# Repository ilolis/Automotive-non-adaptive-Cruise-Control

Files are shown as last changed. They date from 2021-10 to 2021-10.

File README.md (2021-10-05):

# Automotive Non Adaptive Cruise Control retrofit for cars
Specifically designed for a Nissan Micra K12 but can be adapted to other cars with existing PCB and firmware changes. 
**DEVICE UNDER DEVELOPMENT. DO NOT USE IT IN A CAR.**

## Description
The goal of this project is to design an aftermarket KIT that is able to hold the specified speed of a car. 

## How it works
**Inputs**

 - Abs speed sensor signal for measuring speed
 - Brake light signal to detect when brake pedal is pressed
 - Actual accelerator pedal signal 
- Various Buttons for controlling the Cruise Control 

**Outputs**
- The accelerator pedal signal that is routed to the car ECU
- Various indicator lights

How it works:

 -  If the Cruise Control is OFF, the actual accelerator pedal signal is routed to the ECU without the intervention of the KIT. 
 - If the Cruise Control is ON, the Arduino reads the speed of the vehicle through the Speed Sensors and generates the correct pedal signal so that the vehicle maintains set speed. The generated (fake) pedal signal is then routed to the ECU.
 - A MUX is used that outputs either the real accelerator pedal signal (when Cruise Control is disabled) or the (fake) signal of the Arduino (if Cruise Control is enabled).  
 - Two relays connected in series act as a MUX while also providing redundancy. In case one relay is stuck the real accelerator pedal will always be routed to the output.
 - The brake pedal deactivates the Cruise Control and immediately (via hardware logic) changes the Select signal of the MUX so that the output changes to the real accelerator pedal. The system will always switch the output to the real accelerator pedal even if the Arduino is frozen. 

## Status
I am currently testing the board, the functionality works as expected with the prototypes. Never use it in car since it is not 100% tested and I can not guarantee that it works flawlessly. Severe injury can be made. More testing has to be done. Software will be the next step.

## License 
Copyright 2021 Lolis Ilias

Permission is hereby granted, free of charge, to any person obtaining a copy of this software and associated documentation files (the "Software"), to deal in the Software without restriction, including without limitation the rights to use, copy, modify, merge, publish, distribute, sublicense, and/or sell copies of the Software, and to permit persons to whom the Software is furnished to do so, subject to the following conditions:

The above copyright notice and this permission notice shall be included in all copies or substantial portions of the Software.

THE SOFTWARE IS PROVIDED "AS IS", WITHOUT WARRANTY OF ANY KIND, EXPRESS OR IMPLIED, INCLUDING BUT NOT LIMITED TO THE WARRANTIES OF MERCHANTABILITY, FITNESS FOR A PARTICULAR PURPOSE AND NONINFRINGEMENT. IN NO EVENT SHALL THE AUTHORS OR COPYRIGHT HOLDERS BE LIABLE FOR ANY CLAIM, DAMAGES OR OTHER LIABILITY, WHETHER IN AN ACTION OF CONTRACT, TORT OR OTHERWISE, ARISING FROM, OUT OF OR IN CONNECTION WITH THE SOFTWARE OR THE USE OR OTHER DEALINGS IN THE SOFTWARE.

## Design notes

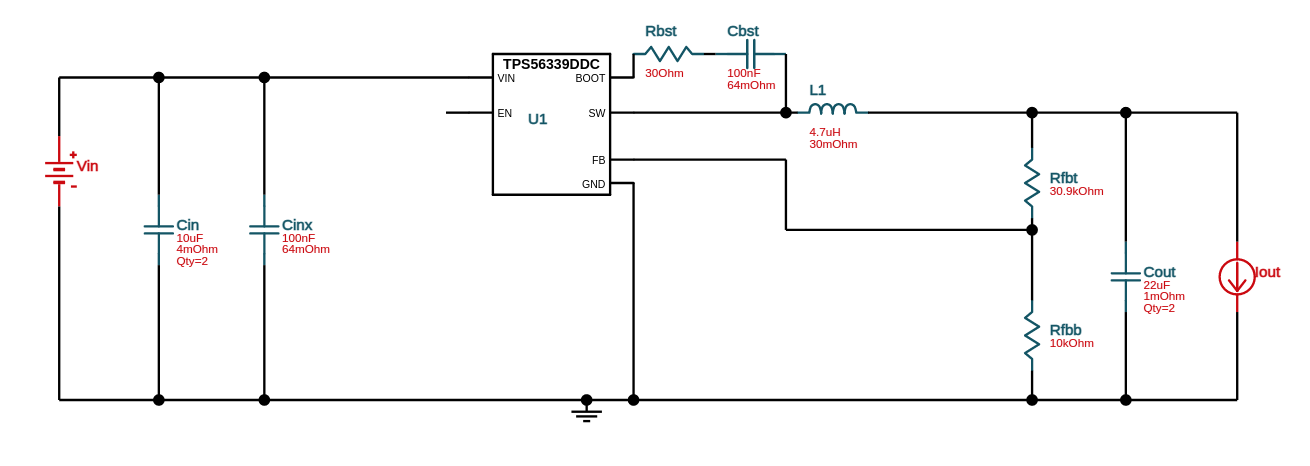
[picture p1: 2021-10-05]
Kicad Schematics/Other/Webench.png

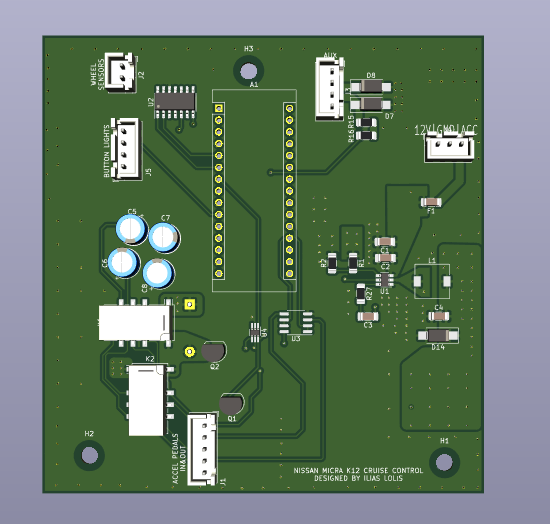
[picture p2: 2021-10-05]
3D Model Front.png

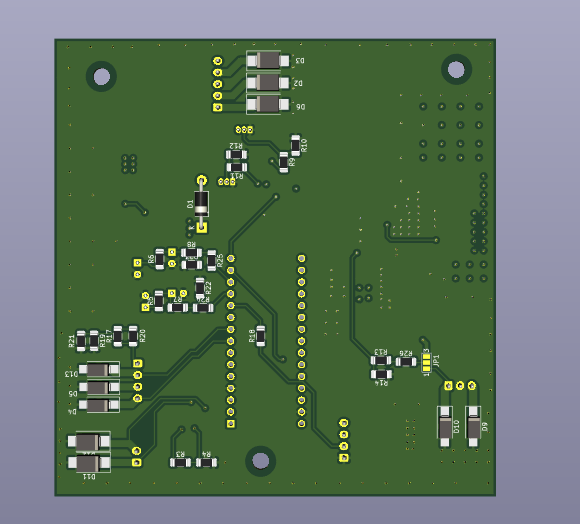
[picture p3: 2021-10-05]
3D Model Bottom.png

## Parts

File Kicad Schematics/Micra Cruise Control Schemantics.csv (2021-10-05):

Reference | Quantity | Value | Footprint | Datasheet | LCSC no | MPN
C1 | 1 | 10uF | Capacitor_SMD:C_1206_3216Metric_Pad1.33x1.80mm_HandSolder | ~ |  | JMK316BJ106KL-T
C2 C3 | 2 | 100nF | Capacitor_SMD:C_1206_3216Metric_Pad1.33x1.80mm_HandSolder | ~ |  | CC1206KRX7R9BB104
C4 | 1 | 22uF | Capacitor_SMD:C_1206_3216Metric_Pad1.33x1.80mm_HandSolder | ~ |  | JMK316BJ226KL-T
C5 C6 | 2 | 2.2uF | Capacitor_THT:CP_Radial_D6.3mm_P2.50mm | ~ | C357599
C7 C8 | 2 | 100uF | Capacitor_THT:CP_Radial_D6.3mm_P2.50mm | ~ | C47891
D1 | 1 | 1N4004 | Diode_THT:D_DO-41_SOD81_P10.16mm_Horizontal | http://www.vishay.com/docs/88503/1n4001.pdf | C331630
D2 D3 D6 D11 D12 | 5 | SMBJ17A | Diode_SMD:D_SMB_Handsoldering |  | C353382
D4 D5 D7 D8 D13 D14 | 6 | SMAJ6.0A | Diode_SMD:D_SMA_Handsoldering |  | C693555
D9 D10 | 2 | SMBJ22A | Diode_SMD:D_SMA_Handsoldering |  | C440288
F1 | 1 | 150mA | Capacitor_SMD:C_1206_3216Metric_Pad1.33x1.80mm_HandSolder | ~ | C369153
K1 K2 | 2 | G6S-2 | Relay_SMD:Relay_DPDT_Omron_G6S-2F | http://omronfs.omron.com/en_US/ecb/products/pdf/en-g6s.pdf |  | G6S-2F DC5
L1 | 1 | 4.7uH | Inductor_SMD:L_7.3x7.3_H3.5 | ~ |  | YPRH0703-4R7M
Q1 | 1 | 2N3904 | Package_TO_SOT_THT:TO-92_Inline | https://www.onsemi.com/pub/Collateral/2N3903-D.PDF | C305395
Q2 | 1 | 2N7000 | Package_TO_SOT_THT:TO-92_Inline | https://www.onsemi.com/pub/Collateral/NDS7002A-D.PDF | C232838
R17 R19 R20 R21 | 4 | 270Ω | Resistor_SMD:R_1206_3216Metric_Pad1.30x1.75mm_HandSolder | ~ |  | 1206W4J0271T5E
R22 R25 | 2 | 4.98k | Resistor_SMD:R_1206_3216Metric_Pad1.30x1.75mm_HandSolder | ~ |  | 1206W4F4991T5E
R23 R24 | 2 | 2.49k | Resistor_SMD:R_1206_3216Metric_Pad1.30x1.75mm_HandSolder | ~ |  | 1206W4F2491T5E
R26 R1 | 1 | 30.9k | Resistor_SMD:R_1206_3216Metric_Pad1.30x1.75mm_HandSolder | ~ |  | 1206W4F3092T5E
R27 | 1 | 30Ω | Resistor_SMD:R_1206_3216Metric_Pad1.30x1.75mm_HandSolder | ~ |  | 1206W4J0300T5E
R3 | 1 | 5kΩ | Resistor_SMD:R_1206_3216Metric_Pad1.30x1.75mm_HandSolder | ~ |  | 1206W4F4991T5E
R4 R5 R6 R7 R8 R11 R15 R16 R18 | 9 | 1kΩ | Resistor_SMD:R_1206_3216Metric_Pad1.30x1.75mm_HandSolder | ~ |  | 1206W4F1001T5E
R9 R10 R12 R13 R14 R2 | 6 | 10kΩ | Resistor_SMD:R_1206_3216Metric_Pad1.30x1.75mm_HandSolder | ~ |  | 1206W4F1002T5E
U1 | 1 | TPS56339DDC | Package_TO_SOT_SMD:TSOT-23-6 | https://www.ti.com/lit/ds/symlink/tps56339.pdf |  | TPS56339DDCR
U2 | 1 | LM339 | Package_SO:SOIC-14_3.9x8.7mm_P1.27mm | https://www.st.com/resource/en/datasheet/lm139.pdf | C71036
U3 | 1 | LM358 | Package_SO:SOP-8_3.76x4.96mm_P1.27mm | http://www.ti.com/lit/ds/symlink/lm2904-n.pdf | C74525
U4 | 1 | NL7SZ57DFT2G | Package_TO_SOT_SMD:SOT-363_SC-70-6_Handsoldering |  | C94398 | NL7SZ57DFT2G
RX | 1 | 100kΩ | Resistor_SMD:R_1206_3216Metric_Pad1.30x1.75mm_HandSolder | ~ |  | 1206W4F1003T5E

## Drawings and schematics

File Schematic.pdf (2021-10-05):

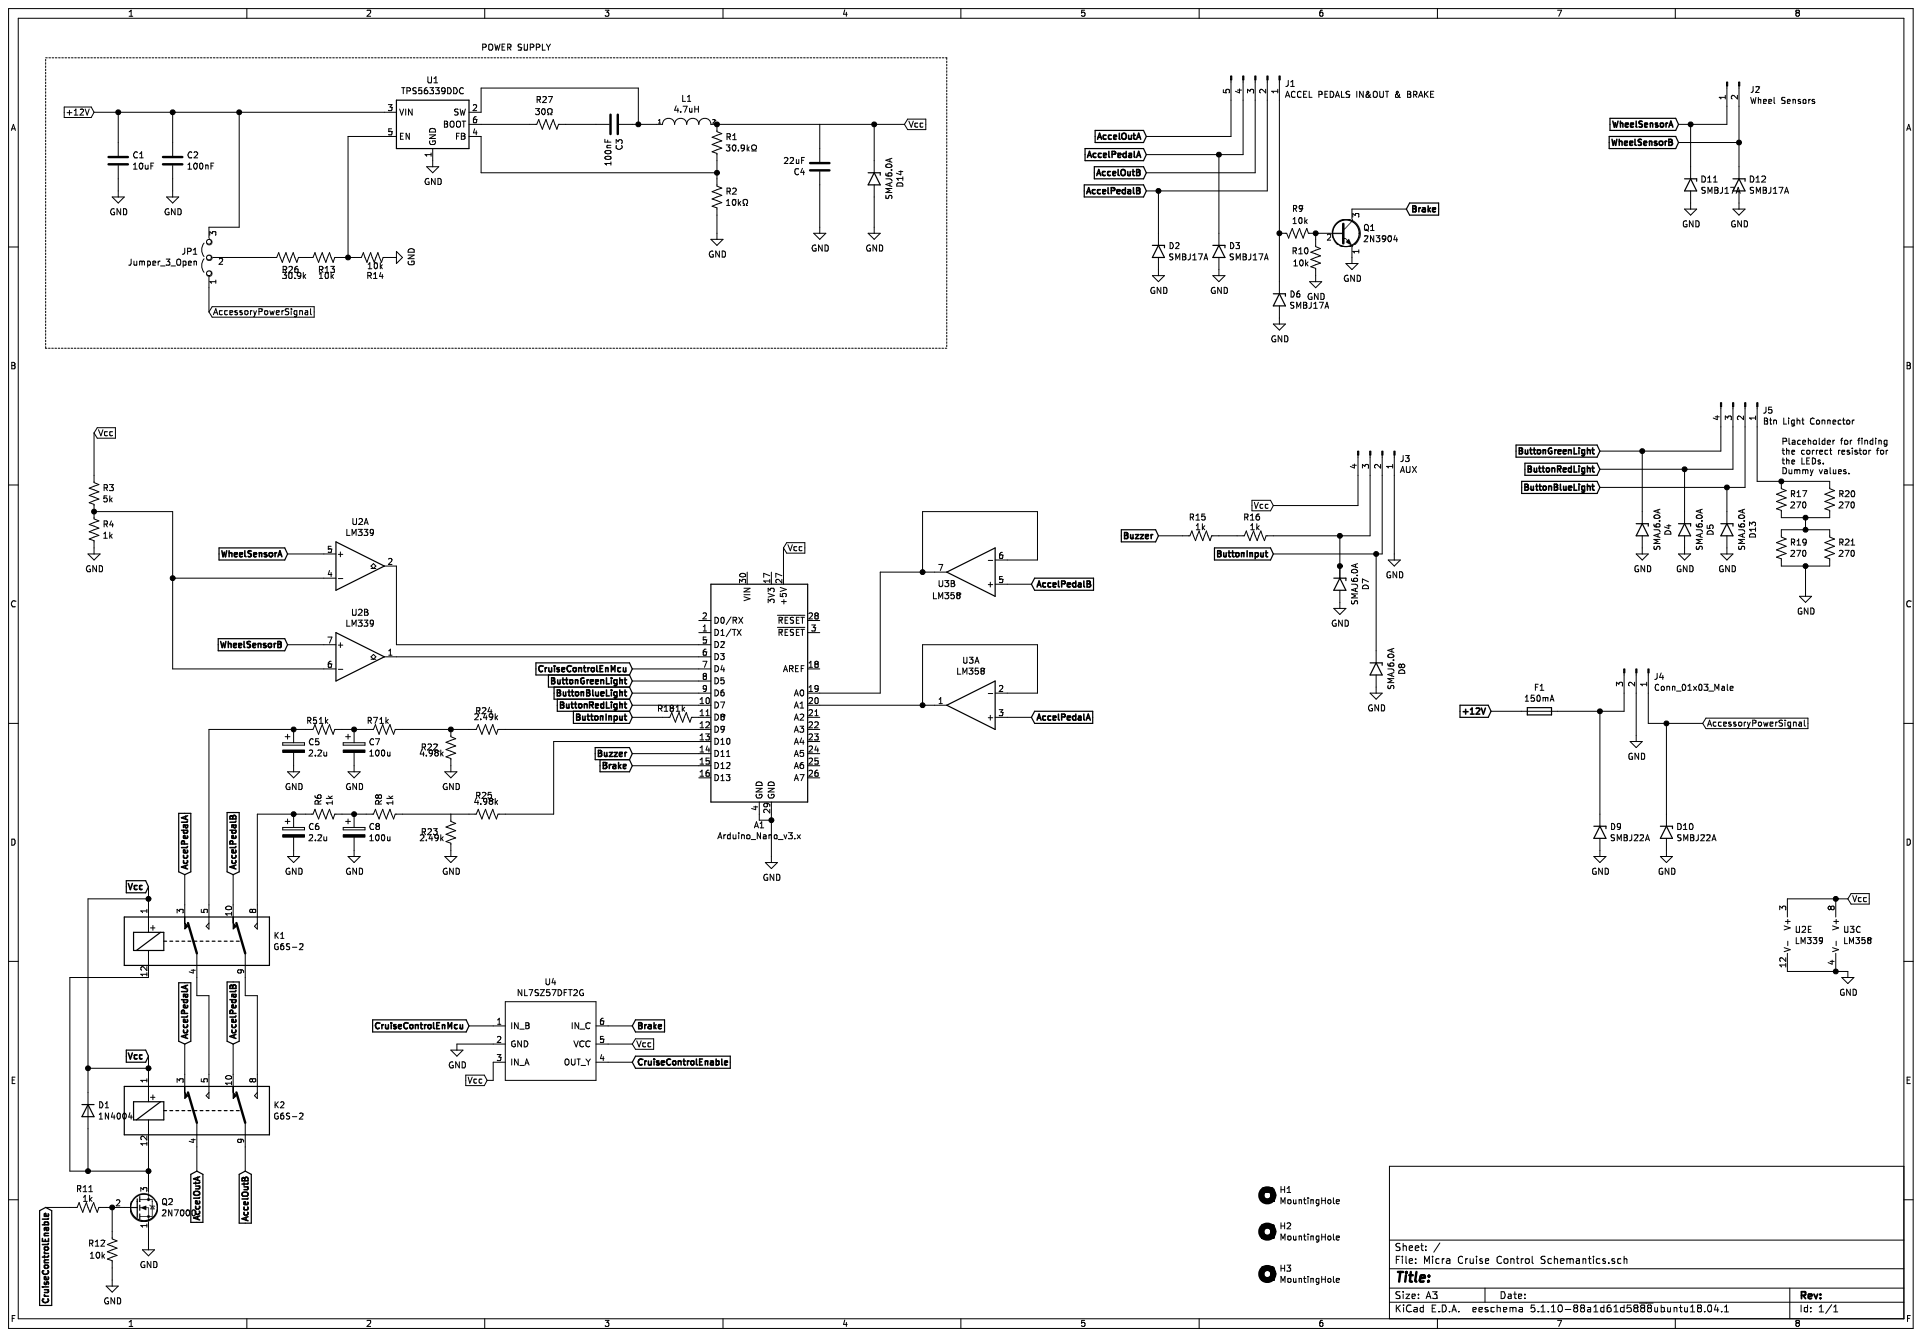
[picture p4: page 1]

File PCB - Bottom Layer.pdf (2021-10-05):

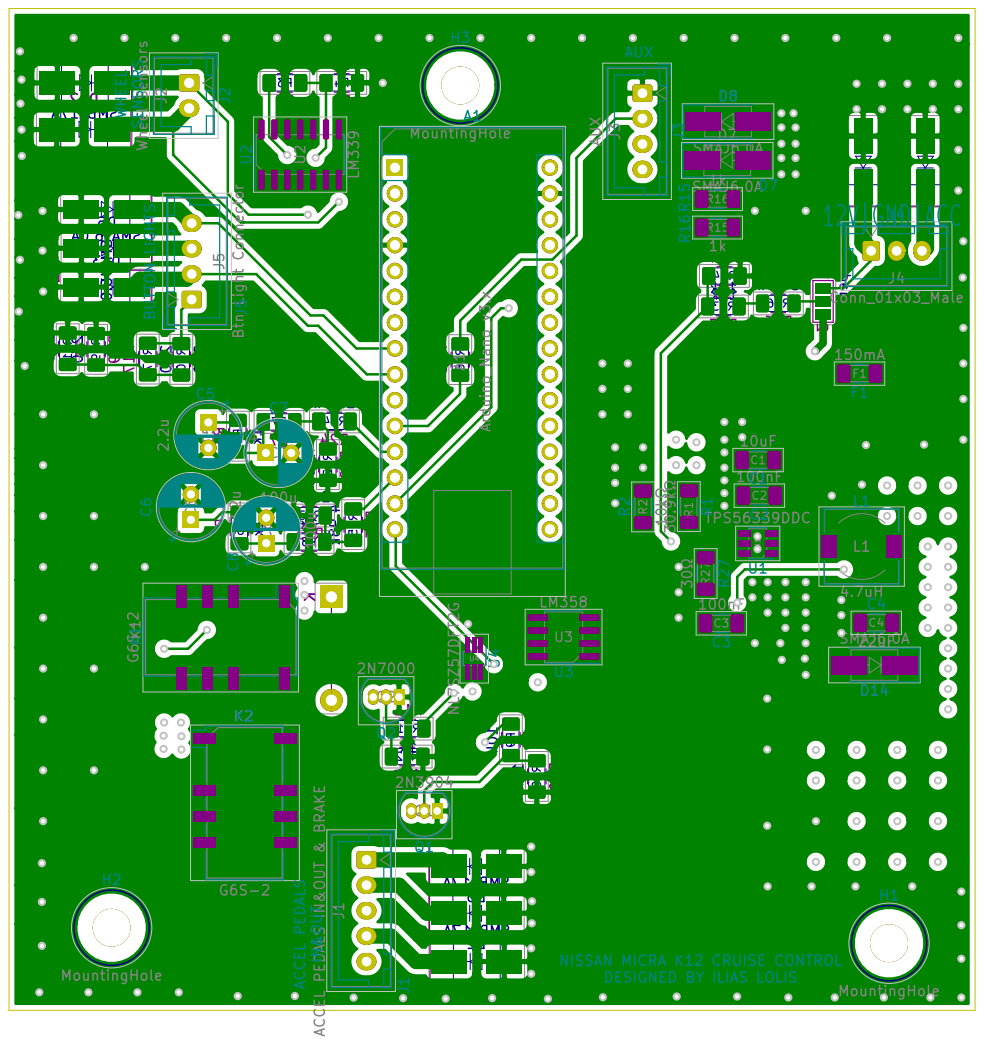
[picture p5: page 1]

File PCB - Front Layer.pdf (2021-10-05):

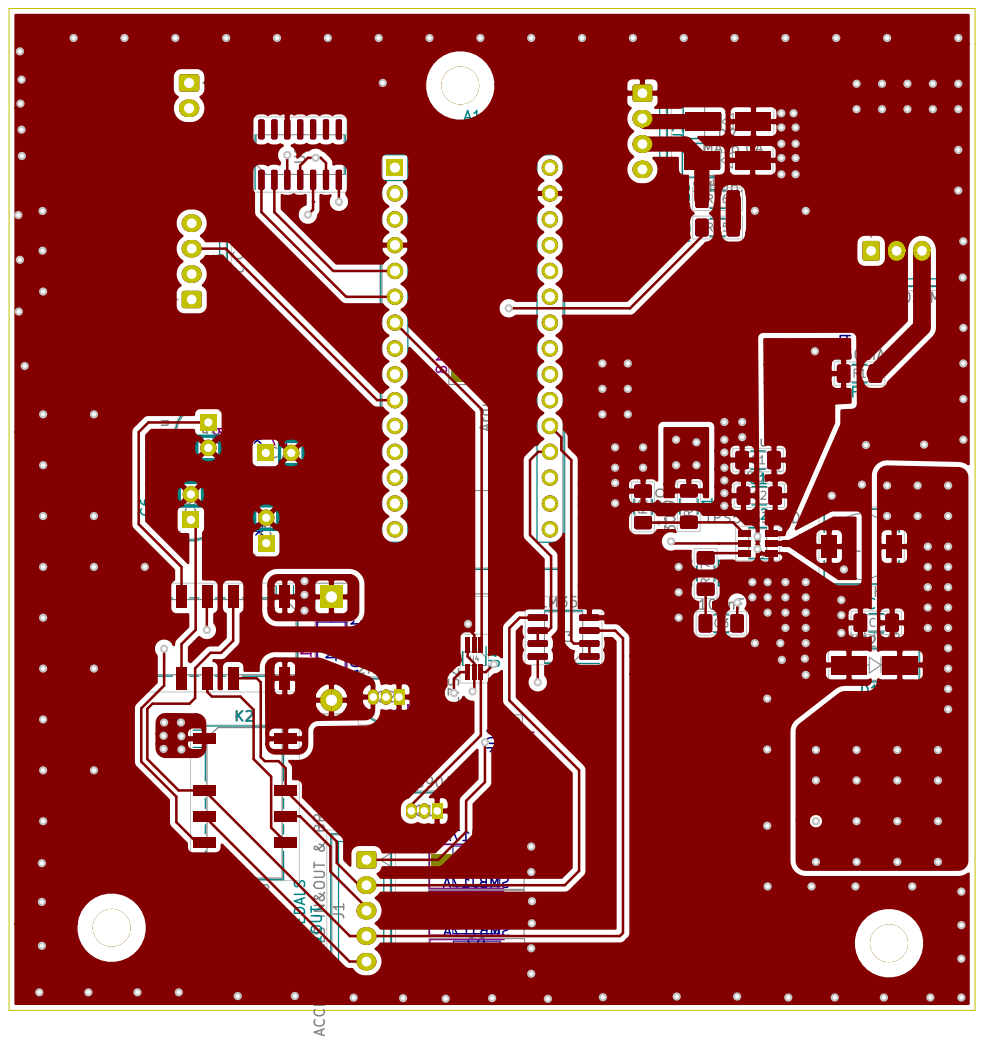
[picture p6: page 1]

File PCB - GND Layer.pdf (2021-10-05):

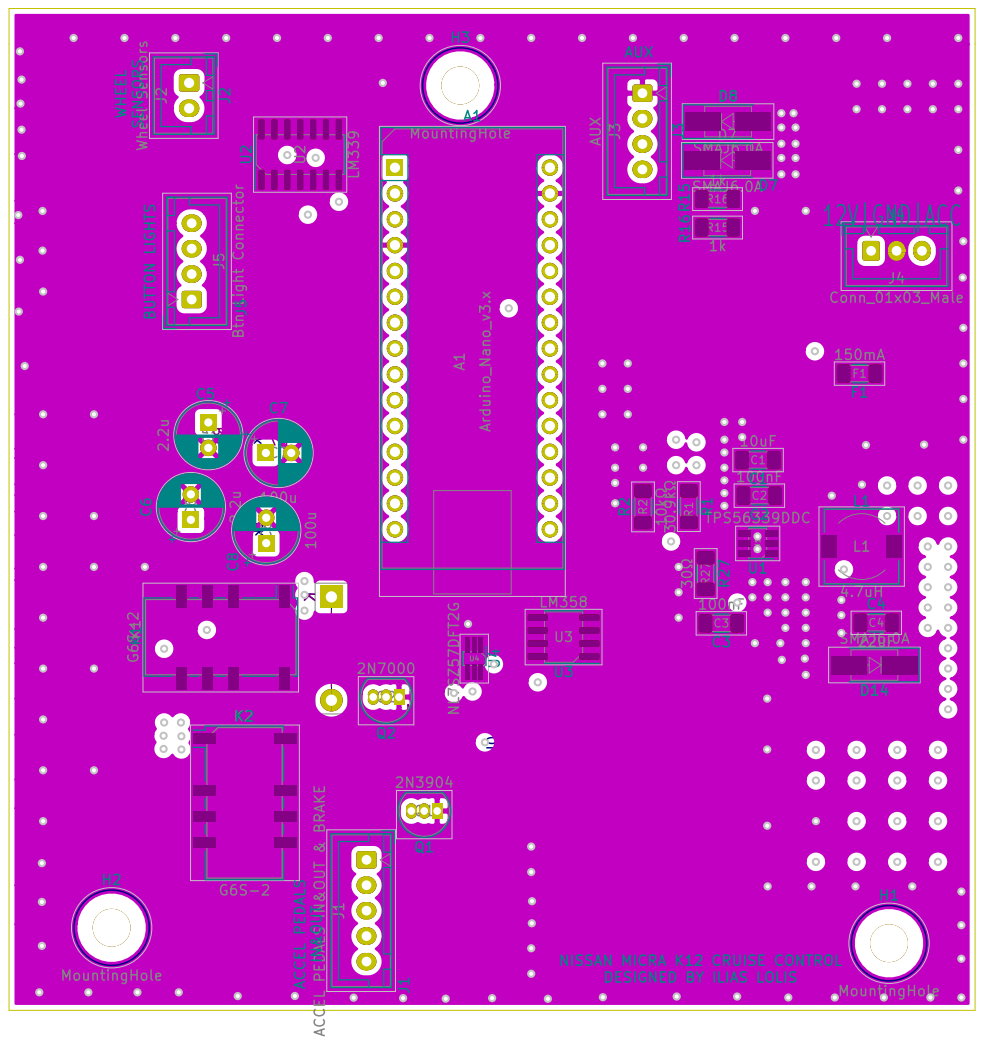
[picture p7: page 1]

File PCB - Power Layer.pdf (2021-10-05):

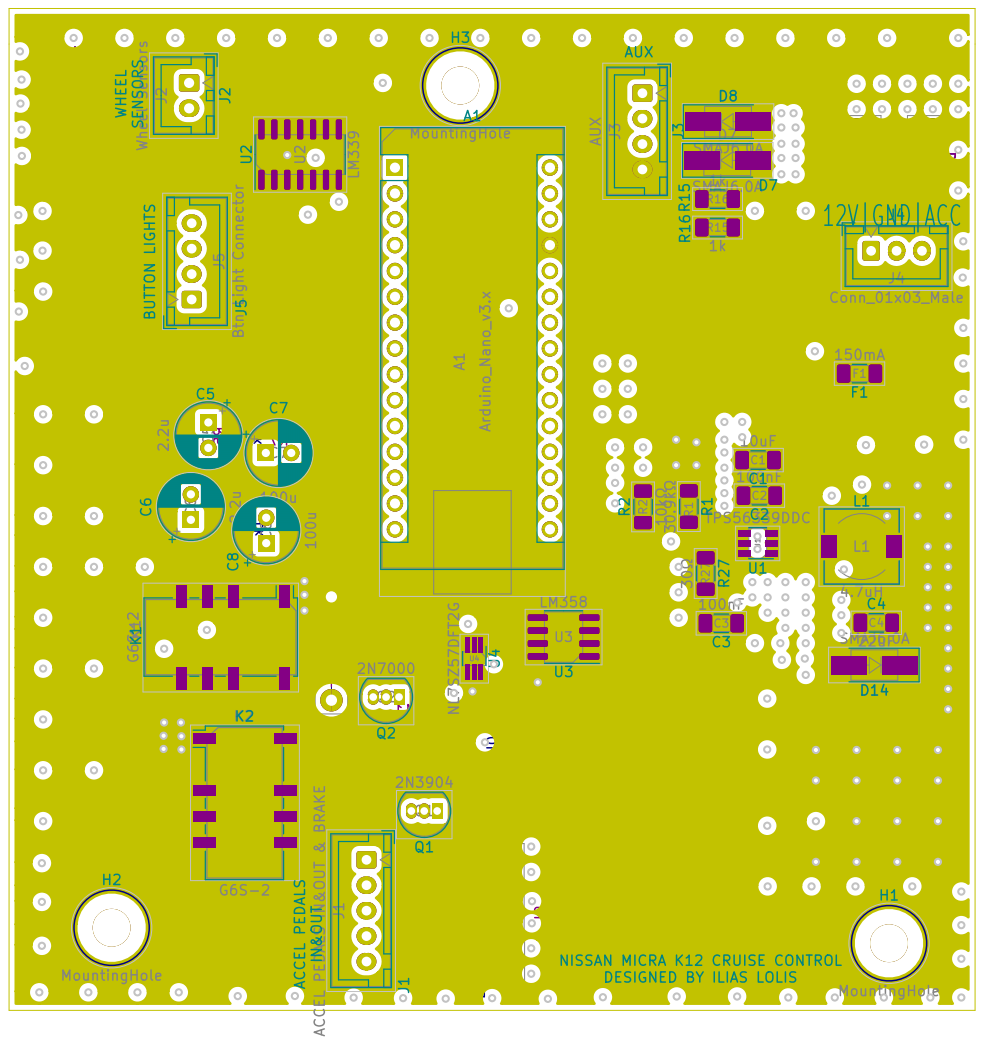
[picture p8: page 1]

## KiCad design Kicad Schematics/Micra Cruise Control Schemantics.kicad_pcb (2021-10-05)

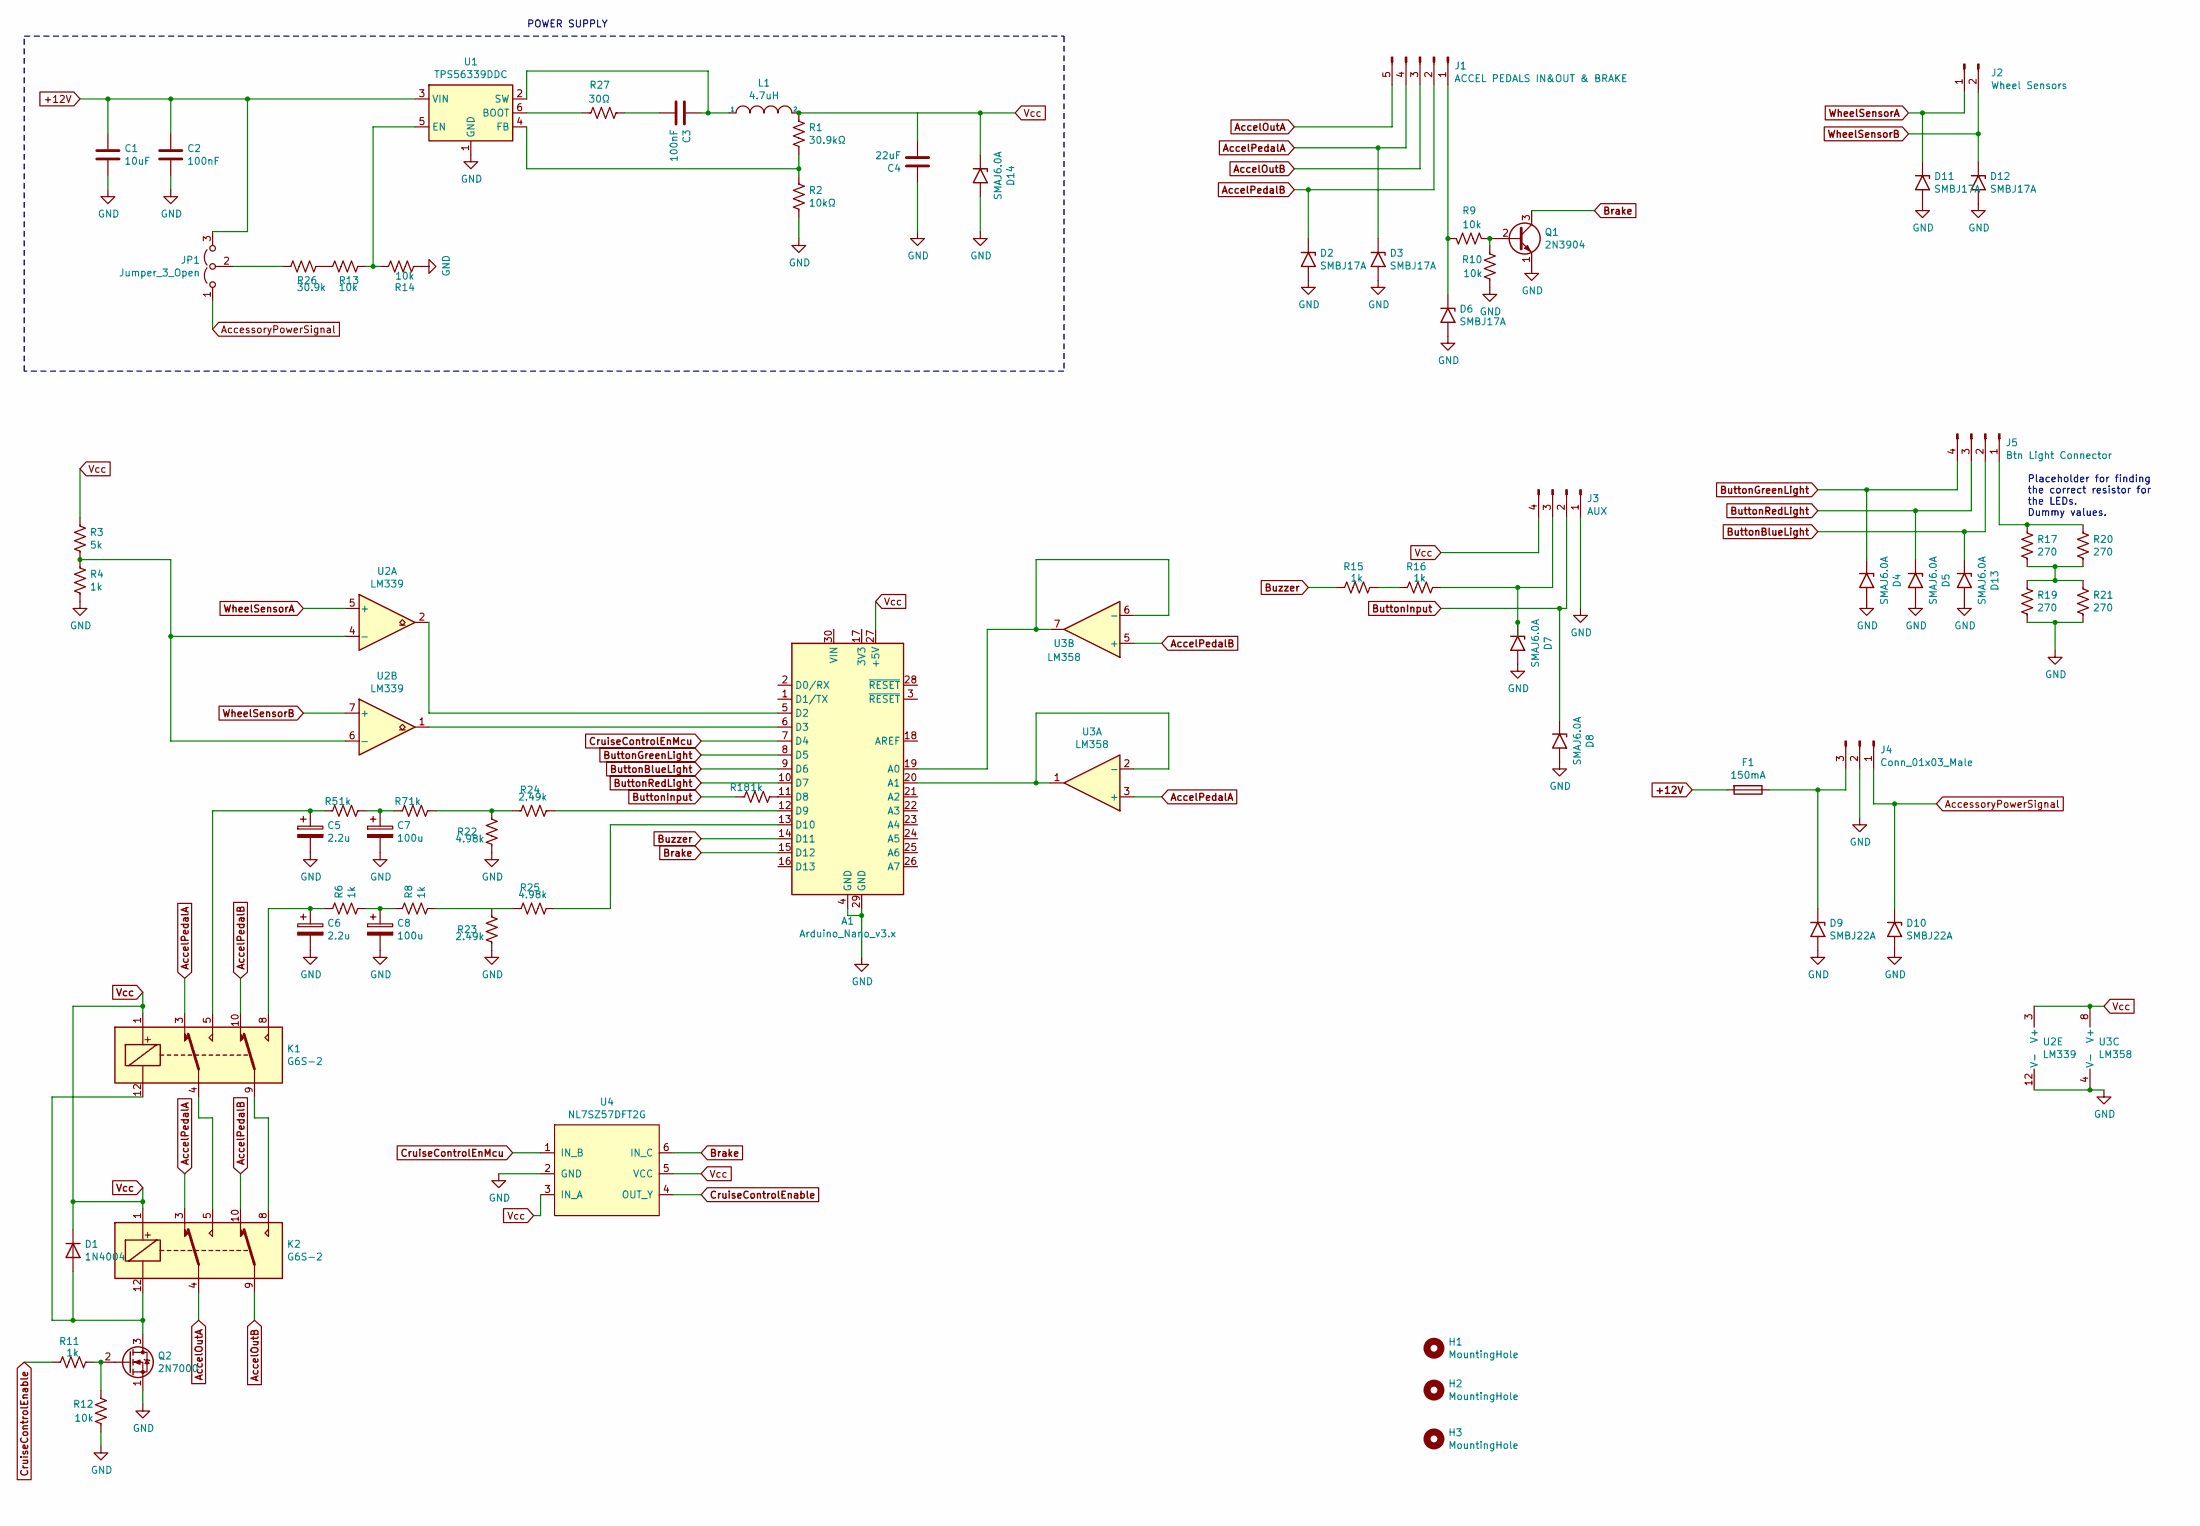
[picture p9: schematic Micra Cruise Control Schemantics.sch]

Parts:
A1: Arduino_Nano_v3.x; Arduino_Nano
C1: 10uF; C_1206_3216Metric_Pad1.33x1.80mm_HandSolder
C2, C3: 100nF; C_1206_3216Metric_Pad1.33x1.80mm_HandSolder
C4: 22uF; C_1206_3216Metric_Pad1.33x1.80mm_HandSolder
C5: 2.2u; CP_Radial_D6.3mm_P2.50mm
C6: 2.2u; CP_Radial_D6.3mm_P2.50mm; PartNo EGS2GM2R2E09OT
C7, C8: 100u; CP_Radial_D6.3mm_P2.50mm; PartNo ERS1EM101E11OT
D1: 1N4004; D_DO-41_SOD81_P10.16mm_Horizontal
D2, D3, D6, D11, D12: SMBJ17A; D_SMB_Handsoldering
D4, D5, D7, D8, D13, D14: SMAJ6.0A; D_SMA_Handsoldering
D9, D10: SMBJ22A; D_SMA_Handsoldering
F1: 150mA; C_1206_3216Metric_Pad1.33x1.80mm_HandSolder; LCSC no C369153
H1, H2, H3: MountingHole; MountingHole_3.7mm
J1: ACCEL PEDALS IN&OUT & BRAKE; JST_XH_B5B-XH-A_1x05_P2.50mm_Vertical
J2: Wheel Sensors; JST_XH_B2B-XH-A_1x02_P2.50mm_Vertical
J3: AUX; JST_XH_B4B-XH-A_1x04_P2.50mm_Vertical
J4: Conn_01x03_Male; JST_XH_B3B-XH-A_1x03_P2.50mm_Vertical
J5: Btn Light Connector; JST_XH_B4B-XH-A_1x04_P2.50mm_Vertical
JP1: Jumper_3_Open; SolderJumper-3_P1.3mm_Open_Pad1.0x1.5mm_NumberLabels
K1, K2: G6S-2; Relay_DPDT_Omron_G6S-2F; PartNo G6S-2F DC5
L1: 4.7uH; L_7.3x7.3_H3.5; Part Number YPRH0703-4R7M
Q1: 2N3904; TO-92_Inline; LCSC no C305395
Q2: 2N7000; TO-92_Inline; LCSC no C232838
R1: 30.9kΩ; R_1206_3216Metric_Pad1.30x1.75mm_HandSolder
R2: 10kΩ; R_1206_3216Metric_Pad1.30x1.75mm_HandSolder
R3: 5k; R_1206_3216Metric_Pad1.30x1.75mm_HandSolder
R4, R5, R6, R7, R8, R11, R15, R16, R18: 1k; R_1206_3216Metric_Pad1.30x1.75mm_HandSolder
R9, R10, R12, R13, R14: 10k; R_1206_3216Metric_Pad1.30x1.75mm_HandSolder
R17, R19, R20, R21: 270; R_1206_3216Metric_Pad1.30x1.75mm_HandSolder
R22, R25: 4.98k; R_1206_3216Metric_Pad1.30x1.75mm_HandSolder
R23, R24: 2.49k; R_1206_3216Metric_Pad1.30x1.75mm_HandSolder
R26: 30.9k; R_1206_3216Metric_Pad1.30x1.75mm_HandSolder
R27: 30Ω; R_1206_3216Metric_Pad1.30x1.75mm_HandSolder
U1: TPS56339DDC; TSOT-23-6; MPN TPS56339DDCR
U2: LM339; SOIC-14_3.9x8.7mm_P1.27mm; LCSC no C71036
U3: LM358; SOP-8_3.76x4.96mm_P1.27mm; LCSC no C74525
U4: NL7SZ57DFT2G; SOT-363_SC-70-6_Handsoldering; MPN NL7SZ57DFT2G; LCSC no C94398

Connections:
+12V: C1.1, C2.1, F1.2, JP1.3 (B), U1.3 (VIN)
AccelOutA: J1.5, K2.4
AccelOutB: J1.3, K2.9
AccelPedalA: D3.1 (A1), J1.4, K1.3, K2.3, U3.3 (+)
AccelPedalB: D2.1 (A1), J1.2, K1.10, K2.10, U3.5 (+)
AccessoryPowerSignal: D10.1 (A1), J4.1, JP1.1 (A)
Brake: A1.15 (D12), Q1.3 (C), U4.6 (IN_C)
ButtonBlueLight: A1.9 (D6), D13.1 (A1), J5.2
ButtonGreenLight: A1.8 (D5), D4.1 (A1), J5.4
ButtonInput: D8.1 (A1), J3.2, R18.1
ButtonRedLight: A1.10 (D7), D5.1 (A1), J5.3
Buzzer: A1.14 (D11), R15.1
CruiseControlEnMcu: A1.7 (D4), U4.1 (IN_B)
CruiseControlEnable: R11.1, U4.4 (OUT_Y)
GND: A1.4 (GND), A1.29 (GND), C1.2, C2.2, C4.1, C5.2, C6.2, C7.2, C8.2, D2.2 (A2), D3.2 (A2), D4.2 (A2), D5.2 (A2), D6.2 (A2), D7.2 (A2), D8.2 (A2), D9.2 (A2), D10.2 (A2), D11.2 (A2), D12.2 (A2), D13.2 (A2), D14.2 (A2), J3.1, J4.2, Q1.1 (E), Q2.1 (S), R2.2, R4.2, R10.1, R12.1, R14.1, R19.2, R21.2, R22.1, R23.1, U1.1 (GND), U2.12 (V-), U3.4 (V-), U4.2 (GND)
unnamed: A1.5 (D2), U2.2
unnamed: A1.6 (D3), U2.1
unnamed: A1.11 (D8), R18.2
unnamed: A1.12 (D9), R24.2
unnamed: A1.13 (D10), R25.2
unnamed: A1.19 (A0), U3.6 (-), U3.7
unnamed: A1.20 (A1), U3.1, U3.2 (-)
unnamed: C3.1, L1.1, U1.2 (SW)
unnamed: C3.2, R27.2
unnamed: C5.1, K1.5, R5.1
unnamed: C6.1, K1.8, R6.1
unnamed: C7.1, R5.2, R7.1
unnamed: C8.1, R6.2, R8.1
unnamed: D1.2 (A), K1.12, K2.12, Q2.3 (D)
unnamed: D6.1 (A1), J1.1, R9.2
unnamed: D7.1 (A1), J3.3, R16.2
unnamed: D9.1 (A1), F1.1, J4.3
unnamed: J5.1, R17.1, R20.1
unnamed: JP1.2 (C), R26.2
unnamed: K1.4, K2.5
unnamed: K1.9, K2.8
unnamed: Q1.2 (B), R9.1, R10.2
unnamed: Q2.2 (G), R11.2, R12.2
unnamed: R1.2, R2.1, U1.4 (FB)
unnamed: R3.2, R4.1, U2.4 (-), U2.6 (-)
unnamed: R13.1, R14.2, U1.5 (EN)
unnamed: R13.2, R26.1
unnamed: R15.2, R16.1
unnamed: R17.2, R19.1, R20.2, R21.1
unnamed: R7.2, R22.2, R24.1
unnamed: R8.2, R23.2, R25.1
unnamed: R27.1, U1.6 (BOOT)
Vcc: A1.27 (+5V), C4.2, D1.1 (K), D14.1 (A1), J3.4, K1.1, K2.1, L1.2, R1.1, R3.1, U2.3 (V+), U3.8 (V+), U4.3 (IN_A), U4.5 (VCC)
WheelSensorA: D11.1 (A1), J2.1, U2.5 (+)
WheelSensorB: D12.1 (A1), J2.2, U2.7 (+)

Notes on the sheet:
Placeholder for finding the correct resistor for the LEDs. Dummy values.
POWER SUPPLY

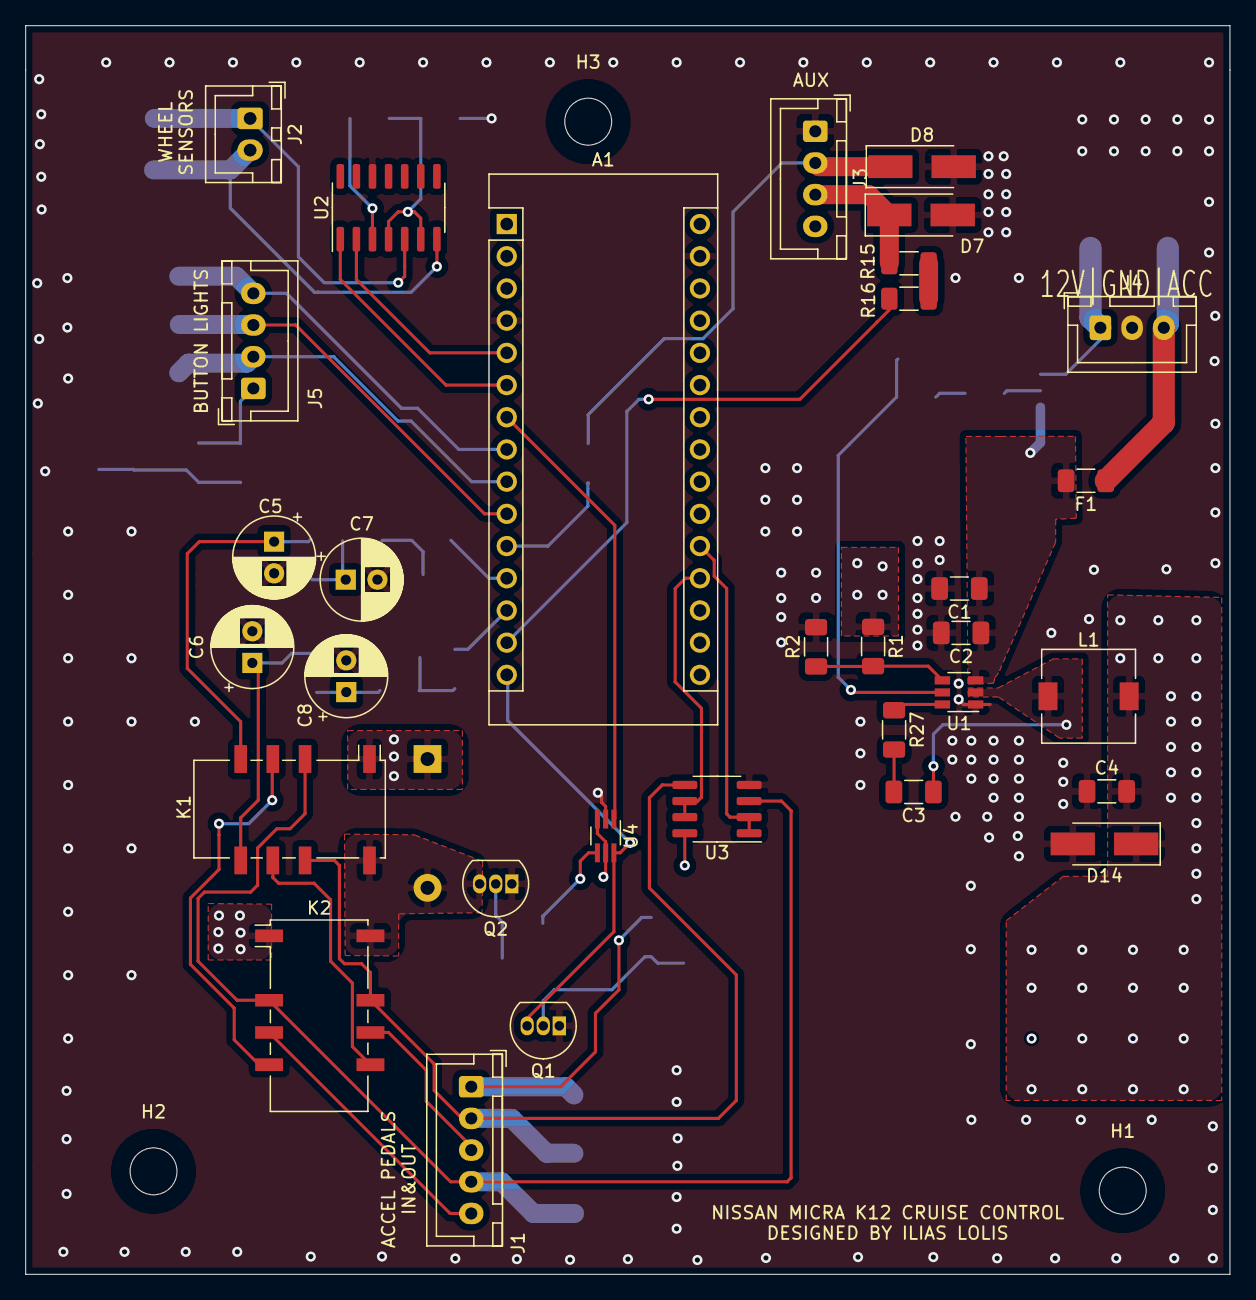
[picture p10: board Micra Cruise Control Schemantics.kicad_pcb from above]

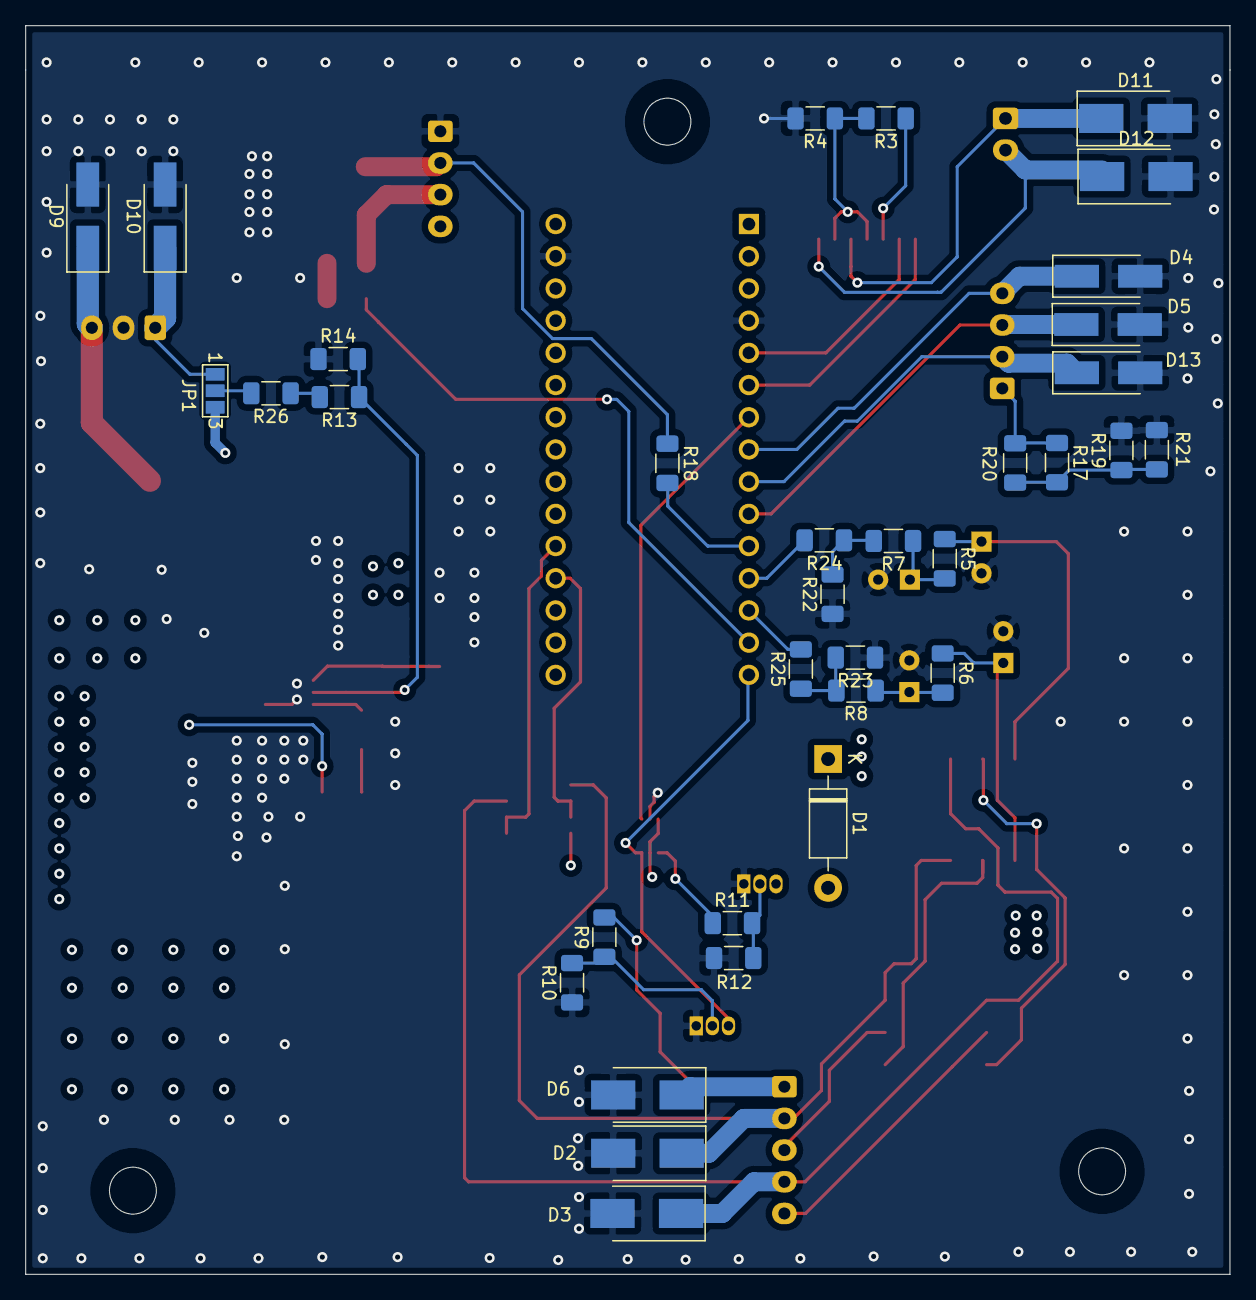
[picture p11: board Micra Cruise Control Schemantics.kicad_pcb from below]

Board: 4 copper layers, 95.0 x 98.5 mm, 69 parts (34 on the bottom side), 50 nets.
